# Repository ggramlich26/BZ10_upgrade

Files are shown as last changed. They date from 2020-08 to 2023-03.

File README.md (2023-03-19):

# Bezzera BZ10 Upgrade
This Project is a replacement for the original Bezzera BZ10 electronics bringing many new features including the following:
- Temperature regulation for boiler and brewing unit
- Volumetric brewing system based on water flow instead of time only
- Standby functionality
- Automated wake up from standby, so that the machine is heated up already when you get up in the morning
- Display of various temperatures, volume distributed and distribution time
- Preinfusion (time based)
- WIFI: All parameters (temperatures, distribution volume, wake up time, etc.) can be set with a smartphone or computer
- Automated cleaning cycle: Ten cycles of switching distribution on and off for 20 seconds each by pressing only one button

## Building the project
This project is set up to be built with Eclipse Sloeber, which adds Arduino support to the Eclipse IDE. It uses the following Libraries, which can be installed through the library manager:
- TFT_eSPI (Version 1.4.16)
- Time (Version 1.5.0)
- MCP23017 (Version	1.1.2), not Adafruit MCP23017!
- PID (Version 1.2.0)
- ADS115_WE (Version 1.3.6)
- ArduinoJson (Version 6.19.4)
- ESPmDNS
- SPIFFS

Some libraries are also added as source code. If you use the Arduino IDE, please move all files from the libraries/library name/src/ directly into your project directory. If you use Sloeber, you might have to add the library paths in the project settings: Right click your project/Properties/"C/C++ Build"/Settings. In the Tool Settings Tab, expand the compiler and click Include Folders. Add the following paths ```"${workspace_loc:/BZ10_upgrade/libraries/AsyncTCP/src}"``` and ```"${workspace_loc:/BZ10_upgrade/libraries/ESPAsyncWebServer/src}"``` under each of the three compilers.

**Board settings:** You need to [install the ESP32 board for Sloeber](http://wiki.lauerbach.de/wiki/view.do?page=ESP32Entwicklungsumgebungen). Select NodeMCU-32S as board, Upload Protocol: Default, Flash Frequency: 40MHz, Upload Speed: 115200

***Windows:*** Under windows you need to make sure you have make command installed (e.g. through MinGW64: select mingw32-make package). You might also have to [install CP2102 drivers](https://www.silabs.com/developers/usb-to-uart-bridge-vcp-drivers) if you get a timeout error when trying to upload your sketch.

**Before building** 
You will additionally need to modify User_Setup.h in the TFT_eSPI library folder. Uncomment `#define ILI9341_DRIVER` (line 39) and make sure all other lines in this block are commented out. Then search for the uncommented pin definitions and change them to the following:
```C++
#define TFT_DC 		23
#define TFT_CS 		17
#define	TFT_MOSI	32
#define	TFT_SCLK	33
#define	TFT_MISO	14
#define TFT_RST		16
```

## Setting your WiFi credentials
The machine can be configured to connect to your own home WiFi network via the web interface:
 1. Turn the machine off.
 2. Set the brewing switch to manual mode, hold both buttons pressed (This step resets the wifi configuration. You can omit it if you have a fresh setup).
 3. Turn the machine on while holding the buttons pressed. You can release them once the screen is ready.
 4. Wait for 30 seconds
 5. Connect with any device to the WiFi network "BZ10" with no password required.
 6. Open your web browser and type 192.168.4.1 into address bar, hit enter.
 7. Now you will be presented a prompt to enter the new SSID (your WiFi name) and password. You can also set your machines Bonjour name. Finish by hitting the "Set" button.

## Connecting to the machine
You can connect to the machine with a browser on any device. You can use your computer, smartphone or tablet, for example. Please note: The machine currently **only supports http and not https**. If you cannot connect, you might have to change the line ine your browser to http://your-ip. There are multiple ways to connect:
### Access point mode
When the machine cannot establish a connection to a wifi network, it automatically creates a hotspot after 30 seconds. Simply connect to the network BZ10 with your device. In the browser type in 192.168.4.1 to go to your machine and change the settings.
### Local WiFi
If the machine is connected to your local WiFi network (little wifi icon shown in the bottom), you can reach it by typing its IP in your browser (use your router configuration website to find out what that is and to make it always the same). Alternatively, you can find it with Bonjour. This works out of the box on Apple and Linux machines and requires an extra [installation from the apple resources](https://support.apple.com/downloads/bonjour-for-windows) on windows. You can then reach the machine by typing bz10.local into your browser. If you want to change the address to something else than bz10, you can modify the Bonjour name on the machine website.
## Usage
Your new espresso machine has a lot more functions than before. This is how you can use them
- **Standard manual distribution:** Flip your distribution switch in the manual distribution position for manual dosing and cooling flush
- **True volumetric distribution:** Flip your distribution switch in the volumetric distribution position for automatic dosing. You can set the desired volume via the website. You will also need to set an offset volume that compensates for the water being moved into the brewing unit but not going through your coffee powder. The best way to do so is to measure the difference between set and actual distribution volume and entering this value via Blynk.
- **Preinfusion:** If you set a preinfusion buildup and wait time on the website, volumetric distribution will come with a preinfusion. This is achieved by turning on the pump for the preinfusion buildup time and then waiting for the preinfusion wait time before starting the actual extraction.
- **Cooling flush:** Since the BZ10 is a HX machine, you will still need to perform a cooling flush just like before the upgrade. But in order to make this process more repeatable, you get a timer showing the time passed after your cooling flush. In order to get this functionality, short press the right button before starting your cooling flush. You will see, that the timer starts counting up once you finished your cooling flush.
- **Standby:** Press the left button shortly to enter standby mode. You can also define a period of time after which the machine will automatically enter standby if it has not been used via Blynk.
- **Automated wake up from standby:** Tired of having to wait for half an hour after getting up until you can finally brew your coffee? Just turn your espresso machine on and press the standby button before going to bed. Now you can set a wake up time via the website. If you set it to half an hour before your alarm goes off, your machine will be all ready for your coffee first thing in the morning. This feature only works if wifi is enabled and the machine has connection to the internet, since it needs to get the current time from a remote server.
- **Automated cleaning cycle:** Cleaning is boring and time consuming task. But now you can save a lot of time. Pressing the right button for 3s or more will start an automated cleaning cycle: Your machine will build up pressure for 20s and then release it for another 20s. This process is repeated 10 times.
- **Disable WiFi:** You got everything set up and don't want your machine to be in the internet any more? Nothing easier than that. Just press the left button for 3s or longer. Now you can see the wifi symbol disappearing from the display and once you restart your machine it won't even connect to your WiFi network any more. To enable WiFi again, just press the left button for 3s or longer again. 
- **Display:** Pretty obvious but you now have a display showing various temperatures, the volume distributed and the time your distribution took (preinfusion time not included). The red circle shows the boiler temperature, the orange circle on the right shows the brewing head temperature and the blue circle in the top shows one additional temperature. I attached this sensor to the tube leading from the heat exchanger to the brewing head.

## Code overview
The machine functionality is based on state machines. There are two state machines for boiler and brewing unit temperature control. Another state machine controls the brewing cycle, one is used for the display, and a last one is responsible for the overall machine state including standby functionality. All state machines are visually shown under `/State machines/State machines.odg`. 
In order to make the program more flexible for other hardware, a hardware abstraction class has been written (`dev.c`). Adapting this class will allow the project to run on a different hardware as well.
Besides machine logic, a faster library for TSIC temperature sensors has been developed.
### Brewing state machine
### Boiler heater state machine
### Brewing unit heater state machine
### Display state machine
### Machine status state machine

## The Hardware
There are eagle layout and gerber files available for a PCB designed with this project. You can simply send those files to a manufacturer such as JLCPCB or Seeedstudio. At the moment I also have a few available from my order, that I could have sent to you for very little money. In case you have trouble soldering SMD (surface mounted device) components, we could also discuss having an assembled PCB shipped to you.
### Hardware on the PCB
You will need all need the components listed below to complete the PCB. All of them can be bought from standard suppliers, including Reichelt, Farnell, Mouser etc.

**Resistors:**
|Value|Package | Quantity | Link |
|--|--|--|--
|2.2k|0603|1
|4.7k|0603|2
|10k|0603|2
|22k|0603|3
|47k|0603|2
|100k|0603|1
220k|0603|2
330k|0603|3
1M|0603|1
4.7M|0603|1

**Capacitors:**
|Value|Package | Quantity | Link |
|--|--|--|--
2.2n|0603|1
10n|0603|2
22n|0603|1
100n|0603|2

**Semiconductors:**
|Name|Package | Quantity | Link |
|--|--|--|--
| **Transistors**|
 IRLML5203|MICRO3|1|[farnell](https://de.farnell.com/infineon/irlml5203trpbf/mosfet-p-kanal-30v-3a-sot23/dp/9103511?st=irlml5203)
 BSS138BK|SOT-23|6|[farnell](https://de.farnell.com/nexperia/bss138bk-215/mosfet-n-kanal-60v-0-36a-sot23/dp/2053833?st=bss138bk)
 **Diodes**|
 BAS21|SOT-23|2|[farnell](https://de.farnell.com/diodes-inc/bas21/schaltdiode-250v-0-25w-sot23-3/dp/1902406?st=bas21)
 **ICs**|
 MCP23017SO|SO28W|1|[farnell](https://de.farnell.com/microchip/mcp23017-e-so/16bit-expander-i-o-i2c-i-f-smd/dp/1332087?st=mcp23017)
 NE555D|SO-8|1|[farnell](https://de.farnell.com/texas-instruments/ne555d/precision-timers-linear/dp/3121191?st=ne555d)
 MCP6002-E/SN|SOIC-8|1|[farnell](https://de.farnell.com/microchip/mcp6002-e-sn/op-verst-rker-1mhz-0-6v-us-4500uv/dp/1332118?st=mcp6002-e/sn)
  ADS1115|MSOP10|1|[e.g. from far east](https://www.aliexpress.com/item/32809831068.html?spm=a2g0s.9042311.0.0.27424c4daHnzqu)

**Boards:**
|Name|Package | Quantity | Link |
|--|--|--|--
| ESP32 nodeMCU with external antenna||1|[from far east](https://www.aliexpress.com/item/4000155919030.html?spm=a2g0s.9042311.0.0.27424c4d4ySog2)|

**Power supply:**
|Name|Package | Quantity | Link |
|--|--|--|--
| HLK-PM01 (5V power supply)||1|[from far east](https://www.aliexpress.com/item/4000534910455.html?spm=a2g0s.9042311.0.0.2f024c4dAwDw9T)|

**Connectors:**
|Name|rows|positions|m/f| Quantity | Comment |
|--|--|--|--|--|--
pinheader 2.54mm|1|2|f+m|4|boiler SSR, boiler probe, NTC, tank switch
pinheader 2.54mm|1|3|f+m|5|connecting TSIC temperature and flow sensors
pinheader 2.54mm|1|6|f+m|2|connecting arduino SSR board
pinheader 2.54mm|1|8|f+m|2|connecting switches and LEDs
pinheader 2.54mm|1|9|f+m|2|display
wire to board connectors, RM5 with screws|1|2|f|1|230V connector [farnell](https://de.farnell.com/camdenboss/ctb1500-2/terminal-block-5mm-2-way/dp/3377326?st=wire%20to%20board%20rm5)

### Hardware off the PCB in the machine
- Arduino SSR board with 4 SSRs (e.g. [Arduino SSR module on Amazon](https://www.amazon.de/Ecloud-4-Channel-Trigger-SSR-Modul-Brett-Arduino-resistivem/dp/B01E6KUMTI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))
- One SSRs for 230V, switchable by 3-5VDC (called SSR-40 DA) for boiler heater and electric brewing unit heater (e.g. [SSR on Amazon](https://www.amazon.de/KKmoon-24V-380V-SSR-40-Relaismodul-Temperaturregler/dp/B010Q6898C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))
- SPI TFT Display 320x240 Pixels with ILI9341 (e.g. [Display on Amazon](https://www.amazon.de/gp/product/B01E0MGZU2/ref=ppx_yo_dt_b_asin_title_o09_s00?ie=UTF8&psc=1))
- Alternative switches: Brewing switch should be replaced by a 3 fixed positions switch, indicator lights should be replaced by push buttons with LEDs, so that they can serve as indicator lights and inputs at the same time. (I used [those](https://www.aliexpress.com/item/4000454624299.html?spm=a2g0s.9042311.0.0.27424c4dZZ9bgU) instead of the indicator lights (3-6V, momentary version) and [those](https://www.aliexpress.com/item/4000028451024.html?spm=a2g0s.9042311.0.0.27424c4dZZ9bgU) for the original two push buttons (5V, latching fixation, blue LED, 2 positions for on/off, 3 positions for brewing switch). If you want to use those switches for on/off, you will need to add a relay in the power supply chain because they are not strong enough for the entire espresso machine power!
- TSIC 306 temperature sensors, 3 pieces
- Flow sensors, 2 pieces (e.g. [from far east](https://www.aliexpress.com/item/32949504762.html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,searchweb201602_,searchweb201603_))
- Quite some wiring. I chose Oelflex Heat for its heat resistance up to 180°C (purchased from Conrad electronics)

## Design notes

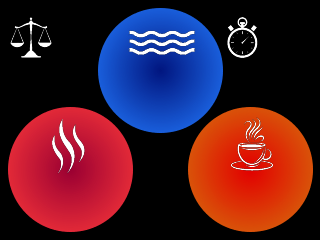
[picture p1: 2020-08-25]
Bilder/Background_V2.png

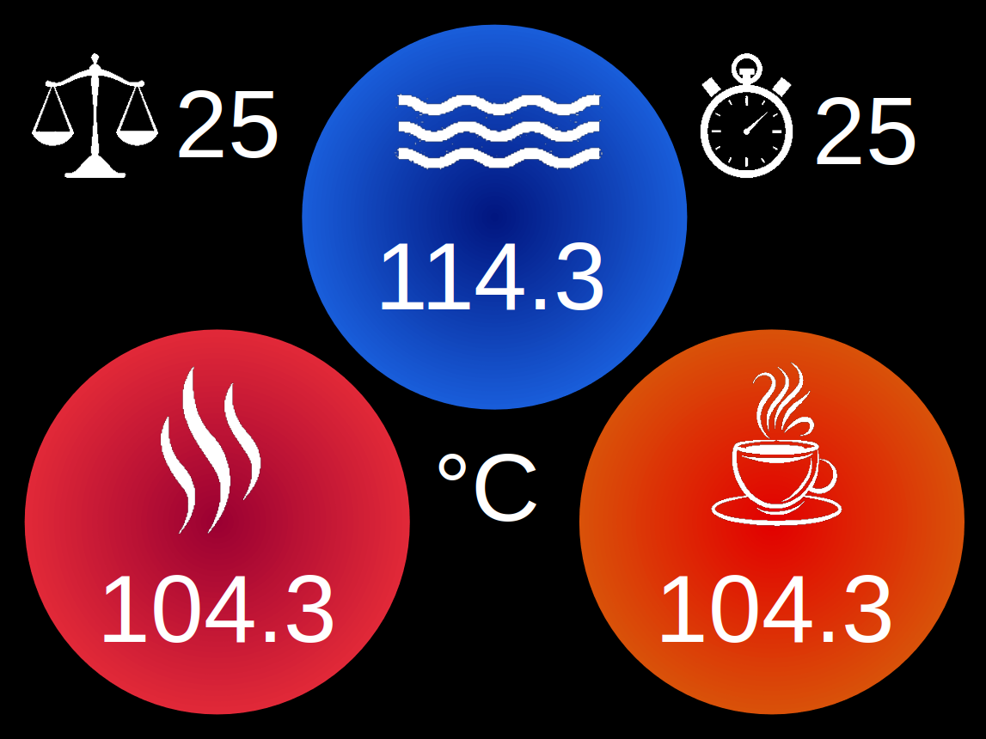
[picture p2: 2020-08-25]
Bilder/Background_V2_with_text.png

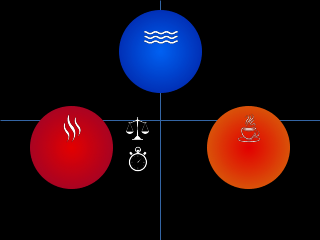
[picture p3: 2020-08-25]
Bilder/Background.png

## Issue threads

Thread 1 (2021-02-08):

TSIC 306 Placement

smoki3, 2021-02-08:
Hi,

very nice project. Could you share a picture where and how you have assembled the TSIC 306? Especially on the boiler and the HX?

ggramlich26, 2021-02-15:
Hi,
thank you. I just added the photos under "images mod/".
I used thermally conductive glue to attach the TSICs and zip ties to hold them in place until the glue had dried. Then I insulated them with mineral wool which I attached with kapton tape (that actually makes a difference of multiple degrees in the measurements).
For the brewing unit I glued the TSIC to a small disk, which I then screwed onto it intead of the original bimetal switch. That's just to sure I could undo my changes in the worst case.
The temperature sensor on the pipe from HX to brewing head is not a big help unfortunately, because the tube slows its reaction down too much. One would probably need to place a sensor inside the tube or the HX boiler itself to get precise measurements.

smoki3, 2021-02-15:
Okay thanks for the pictures :) How is your experience with the temp sensor outside the boiler? The BZ07 for example uses a tube which goes into the boiler to measure the temperatur

Do you also have the layout ready for the pcb, or you maybe have one pcb remaining?  I also bought a BZ10 and want to mod it too.

ggramlich26, 2021-02-18:
A temp sensor inside the boiler certainly is the better option but it I didn't want to dril a hole in my boiler. Placing the sensor outside the boiler adds a noticable latency.

I can add the layout for the PCB but the current version still uses an ESP32 board with integrated antenna. Since the metallic case of the machine acts as a faraday cage, you'd have very bad intenet connection in there. I just cut the antenna off and soldered a coaxial wire with SMA connector to it. I then lead it out of the machine and attached a regula WiFi antenna.
I can also send you a PCB. I think I have four left atm.

Reisediel, 2023-01-21:
I got a BZ10 shortly and I want to mod it. For temp measurement inside the boiler you can unscrew screw #1 and replace it with an 1/4" probe like in the boiler from a BZ07.
https://www.avola-coffeesystems.de/bezzera/bezzera-bz10-heizung/8279034

smoki3, 2023-01-21:
Yes correctly

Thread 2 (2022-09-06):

Capacity C7 / C8

smoki3, 2022-09-06:
Hi,

do you know the value of the capacity c7/c8?

ggramlich26, 2022-09-08:
Hi,

I had paced them there to have the possibility to smoothen the temperature sensor voltages in case there was a lot of noise coming from the power supply etc but didn't end up using them. You can leave them empty, that's why there are no values given.

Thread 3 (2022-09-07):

Blynk Legacy wird abgeschaltet.

smoki3, 2022-09-07:
Hi,

das bisher genutzte Blynk wird ja bald abgeschaltet. Hast du dir schon eine alternative überlegt oder auf das neue zu migrieren?

ggramlich26, 2022-09-08:
Hi,

ja, das ist mir leider auch schon aufgefallen. Ich will eigentlich nicht auf das neue migrieren, weil das in einem Abo-Modell läuft und mir das einfach zu teuer ist, ich hatte aber auch noch keine Zeit mich um eine gute Alternative zu kümmern. Hast du zufällig eine Idee?

smoki3, 2022-09-08:
Ich bin nun auf das neue migriert. Gibt ein paar Widget die kostenlos sind. Ich benutze hauptsächlich den Slider. Kann in meinem Fork anschauen.

smoki3, 2022-09-08:
So sieht das ganze dann aus:

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

ggramlich26, 2022-09-13:
Das sieht gut aus! Und davon ist noch alles kostenlos?

smoki3, 2022-09-13:
Ja genau dafür musste ich nun gar nix bezahlen. Eine ganze Reihe kostenloser Widget. Damit lässt sich die Steuerung ganz gut realisieren.

Das ist die Mobile Ansicht:

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

ggramlich26, 2022-09-14:
Perfekt, was will ich mehr! Dann werde ich mal in deinen code reinschauen für die Portierung und mich bis Ende des Jahres darum kümmern selbst auch umzusteigen. Danke für die Idee!

smoki3, 2022-09-14:
Am code ändert sich eigentlich nichts. Außer die Zugangsdaten müssen ergänzt werden und die aktuelle Library

smoki3, 2022-09-14:
Die meiste Arbeit ist das Anlegen des Templates

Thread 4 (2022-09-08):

Widerstände Boiler Füllstand

smoki3, 2022-09-08:
Hi,

ich wollte nun auch auf die neue Platine umsteigen. Allerdings funktioniert bei mir die Füllstandsonde nicht mehr.

Nun hab ich in LTSpice, Board V2 und V3 jeweils unterschiedliche Werte. Kann du mir da einwenig Licht ins dunkle bringen und mir die Korrekten werte nennen?

smoki3, 2022-09-13:
Konnte es inzwischen beheben. War wohl irgendwo ein falscher Widerstand

ggramlich26, 2022-09-14:
Super, das freut mich!

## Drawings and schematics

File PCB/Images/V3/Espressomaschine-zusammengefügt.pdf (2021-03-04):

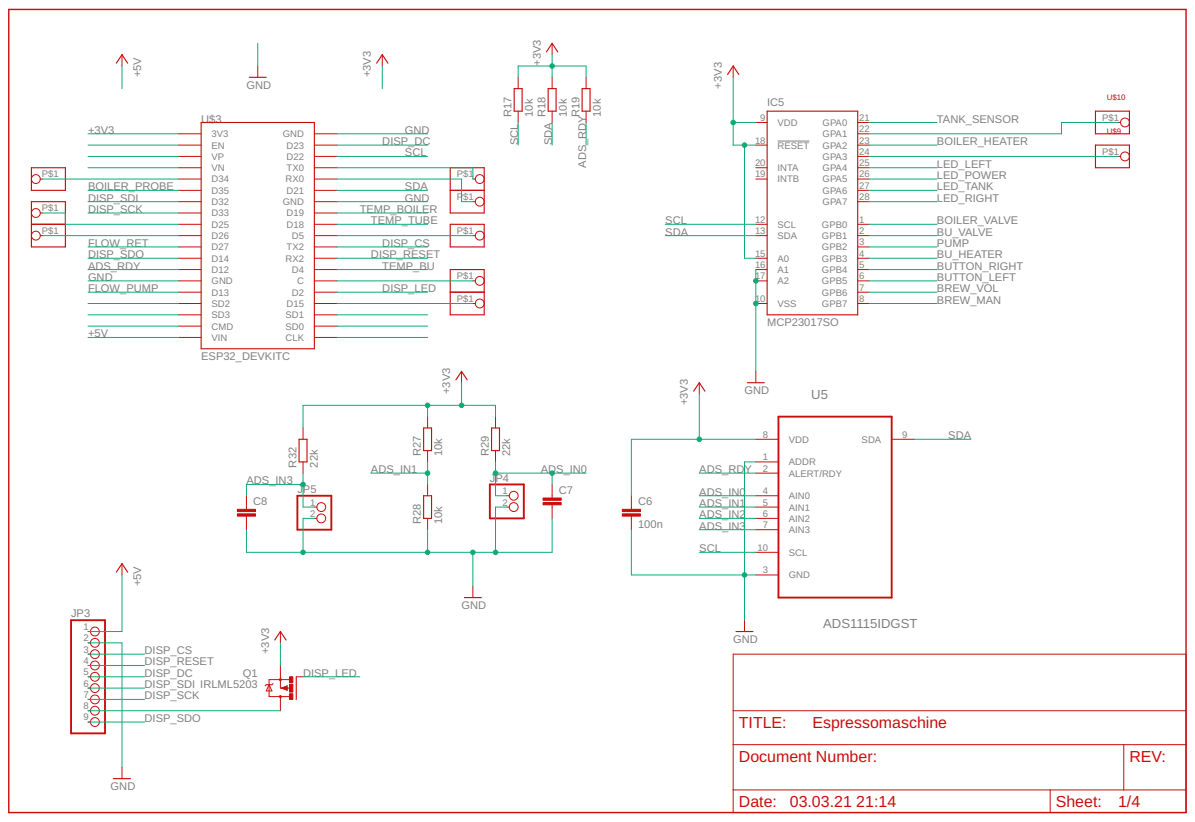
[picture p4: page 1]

Document Number: | REV:

Date: 03.03.21 21:14 | Sheet: 1/4

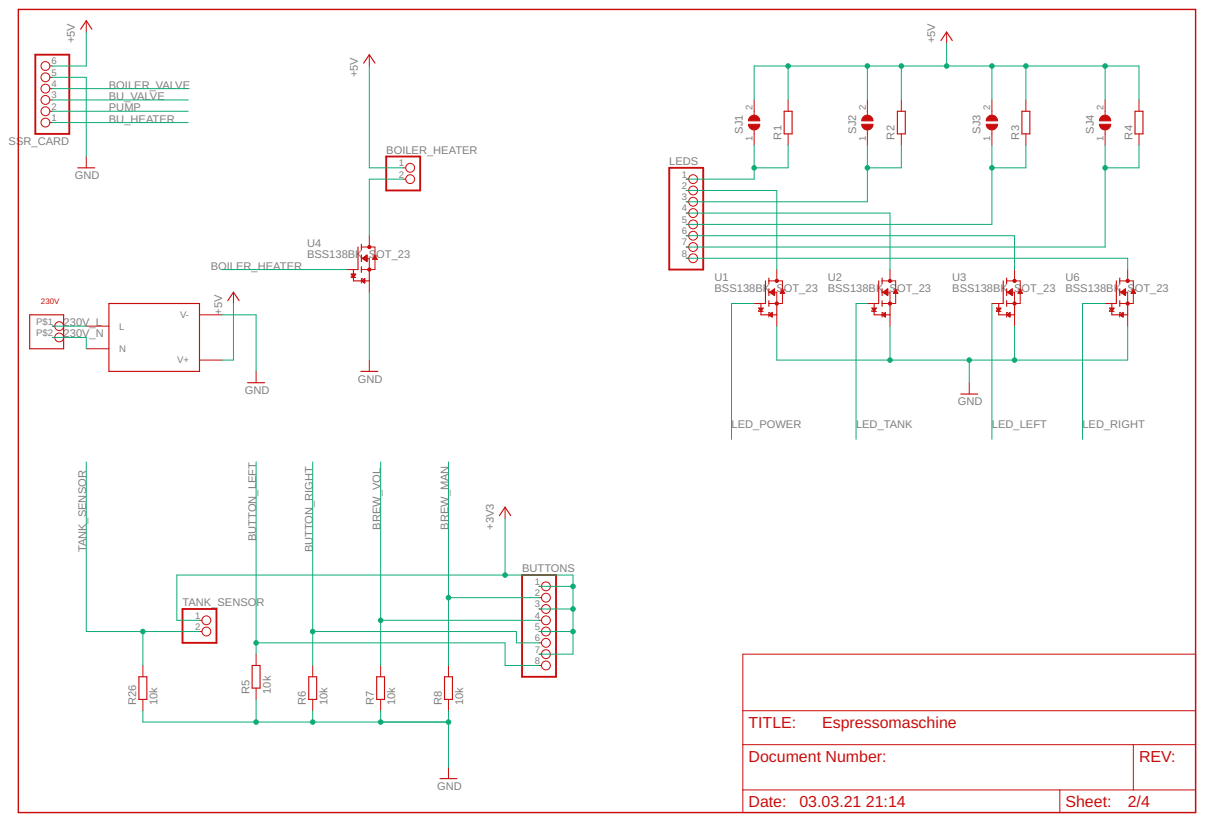
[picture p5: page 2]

Document Number: | REV:

Date: 03.03.21 21:14 | Sheet: 2/4

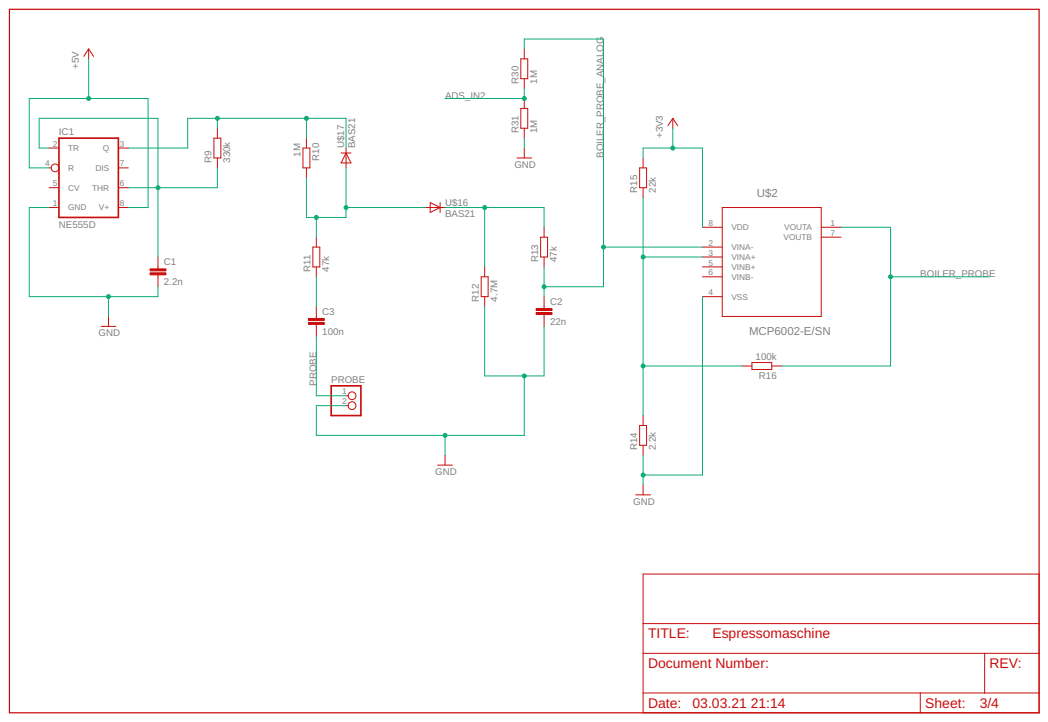
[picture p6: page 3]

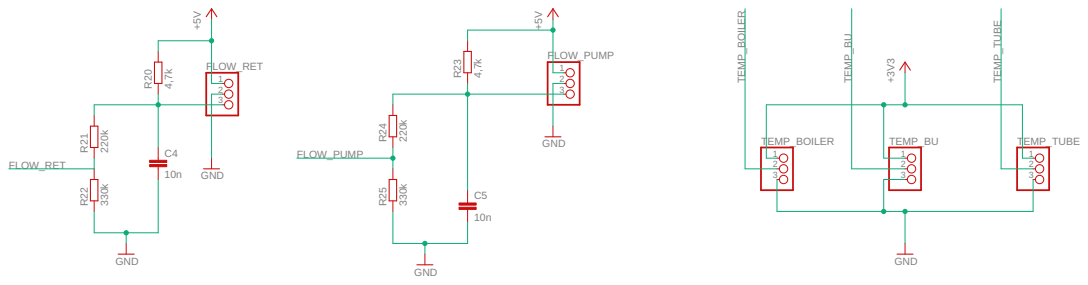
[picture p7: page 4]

Document Number: | REV:

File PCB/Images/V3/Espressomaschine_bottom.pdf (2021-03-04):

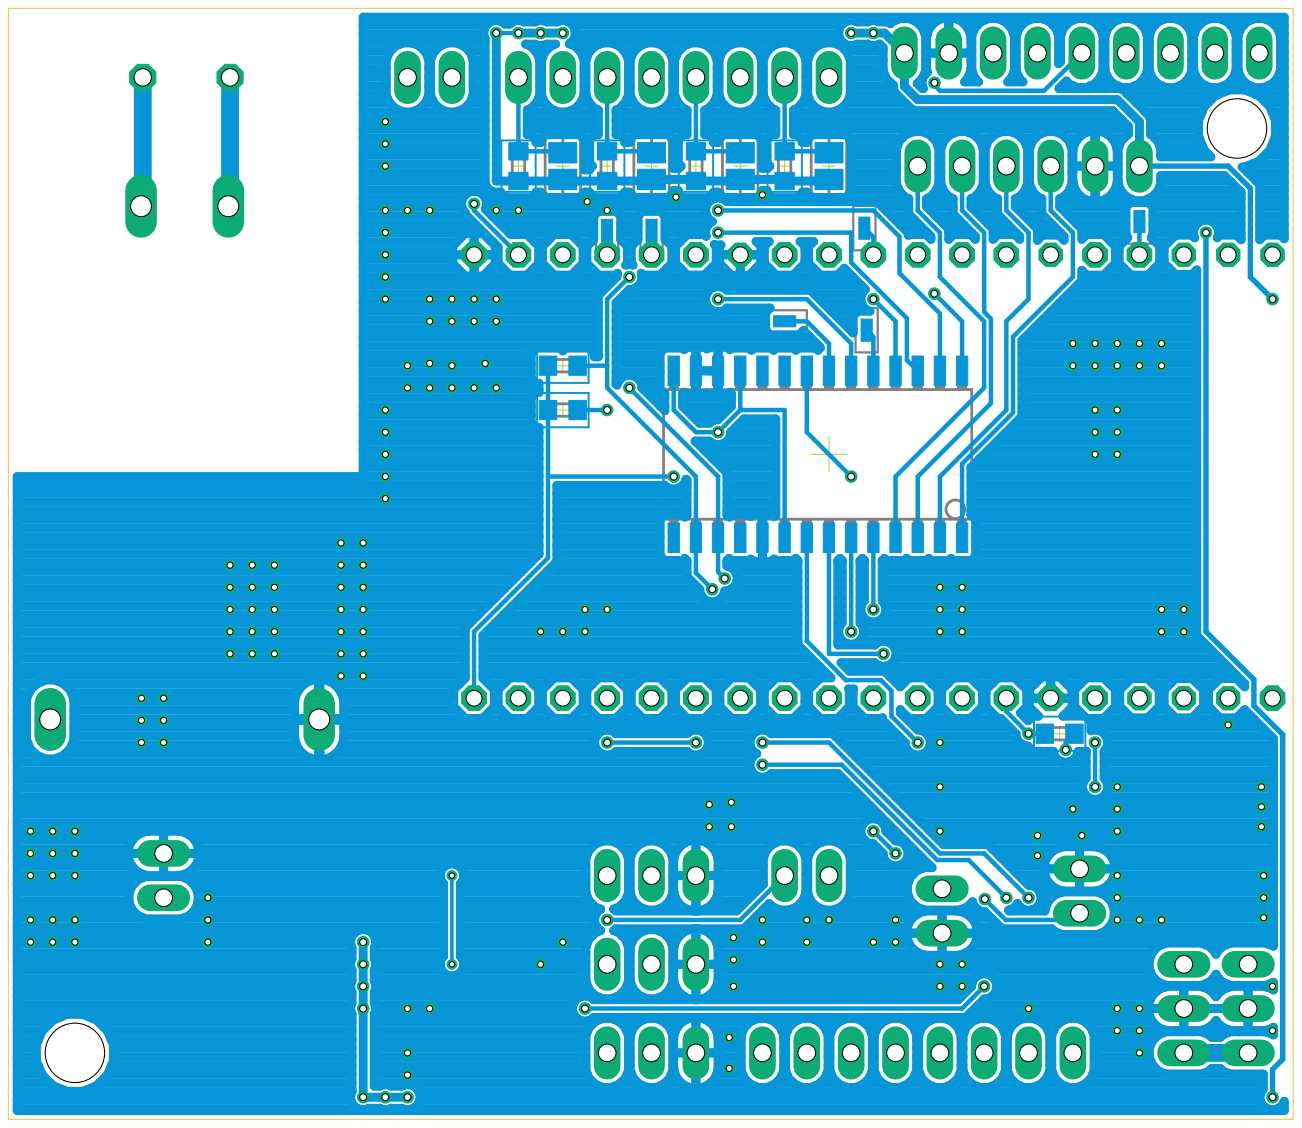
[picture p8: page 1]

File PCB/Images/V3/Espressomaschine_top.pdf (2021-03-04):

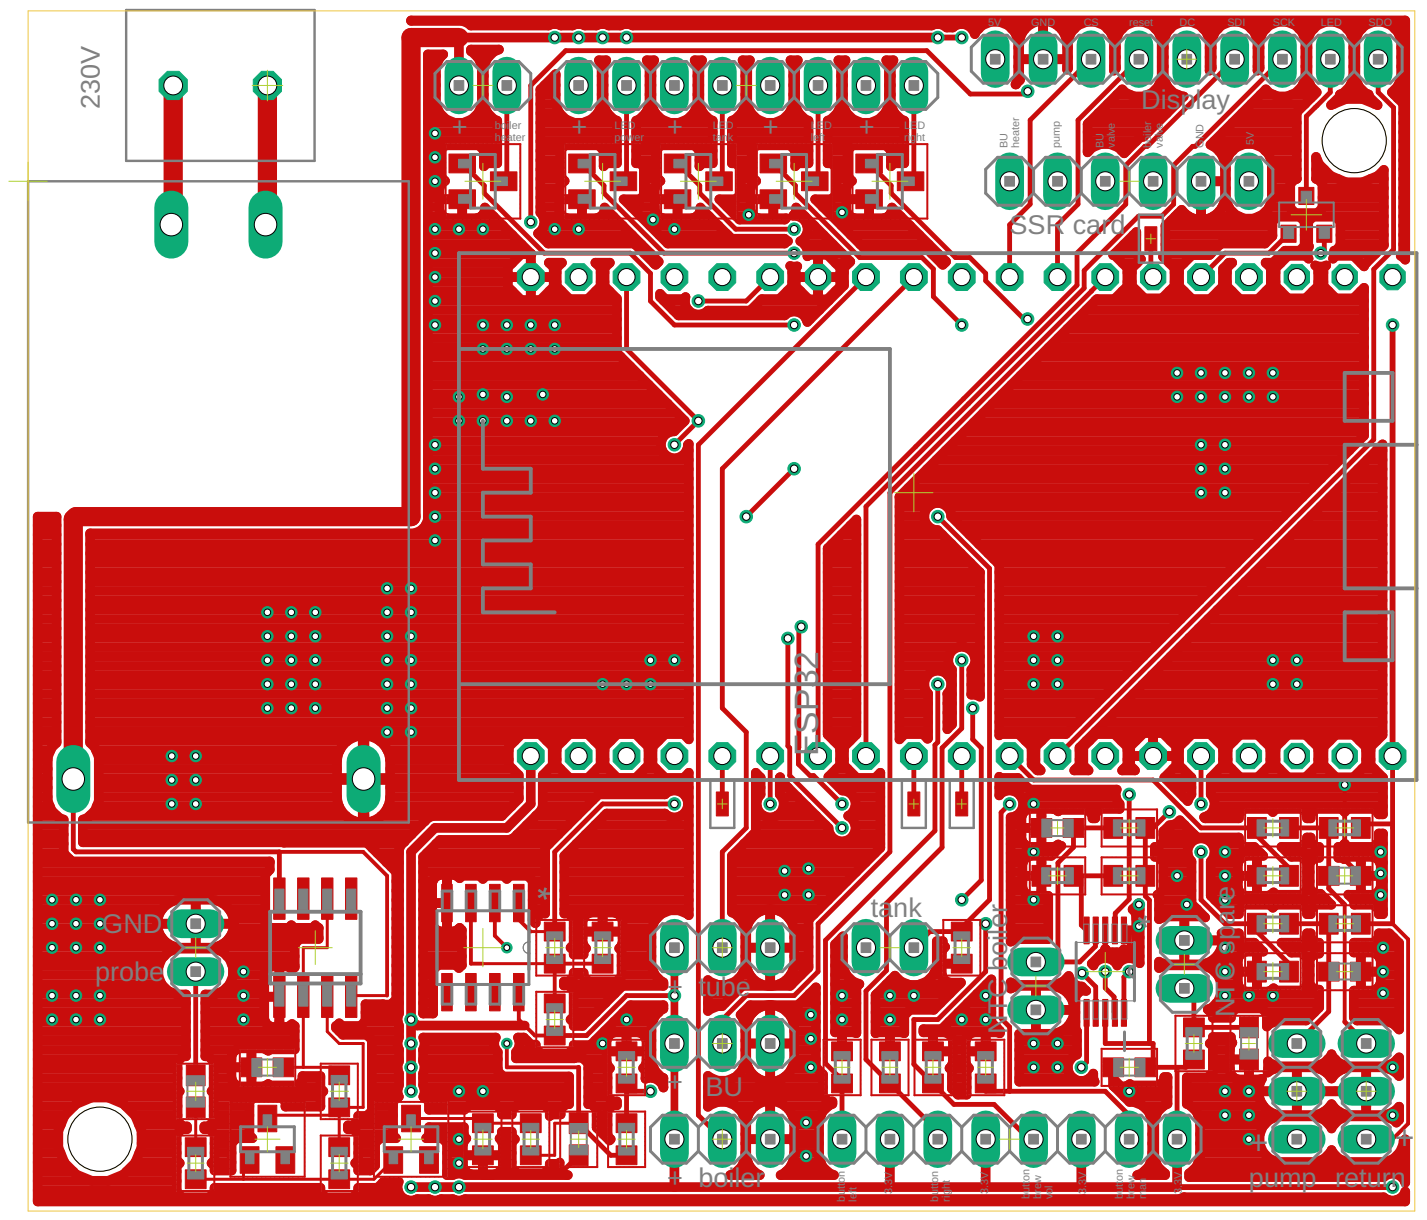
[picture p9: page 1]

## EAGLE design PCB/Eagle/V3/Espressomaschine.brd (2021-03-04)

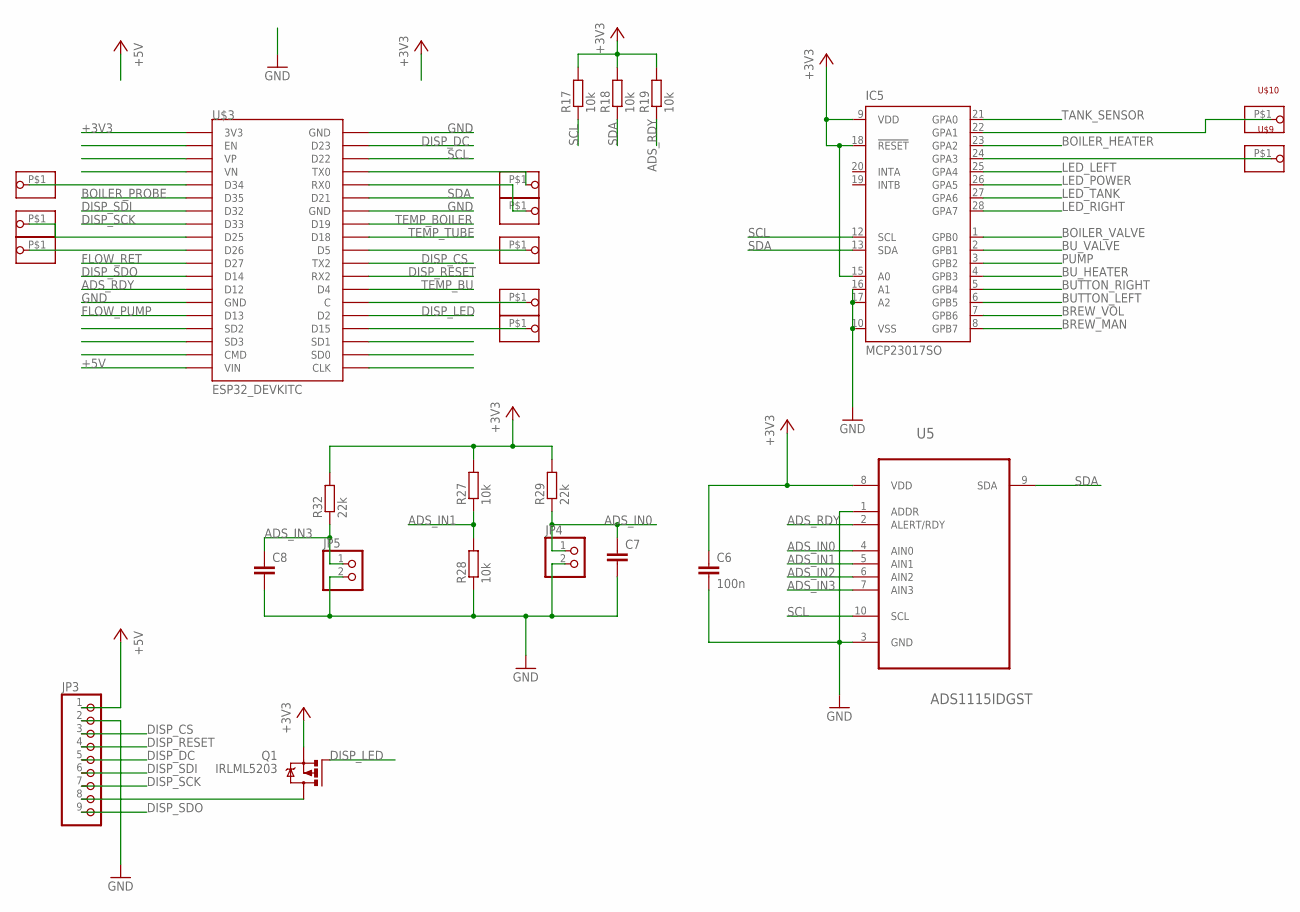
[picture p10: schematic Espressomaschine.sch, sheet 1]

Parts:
C6: 100n; C0603
C7, C8: C-EUC0603; C0603
IC5: MCP23017SO; SO28W
JP3: PINHD-1X9; 1X09
JP4, JP5: PINHD-1X2; 1X02
Q1: IRLML5203; MICRO3
R17, R18, R19, R27, R28: 10k; R0603
R29, R32: 22k; R0603
U5: ADS1115IDGST; SOP50P490X110-10N
U$3: ESP32_DEVKITC
U$5, U$6, U$7, U$8, U$9, U$10, U$11, U$12, U$13, U$14: PINHD-1X1SMD_RM1.27; 1X01_SMD_RM1.27

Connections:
+3V3: C6.1, IC5.9 (VDD), IC5.15 (A0), IC5.18 (!RESET), Q1.2 (S), R17.2, R18.2, R19.2, R27.2, R29.2, R32.2, U5.8 (VDD), U$3.3V3; also elsewhere on the board
+5V: JP3.1, U$3.VIN; also elsewhere on the board
ADS_IN0: C7.1, JP4.1, R29.1, U5.4 (AIN0)
ADS_IN1: R27.1, R28.2, U5.5 (AIN1)
ADS_IN2: U5.6 (AIN2); also elsewhere on the board
ADS_IN3: C8.1, JP5.1, R32.1, U5.7 (AIN3)
ADS_RDY: R19.1, U5.2 (ALERT/RDY), U$3.D12
BOILER_HEATER: IC5.23 (GPA2); also elsewhere on the board
BOILER_PROBE: U$3.D35; also elsewhere on the board
BOILER_VALVE: IC5.1 (GPB0); also elsewhere on the board
BREW_MAN: IC5.8 (GPB7); also elsewhere on the board
BREW_VOL: IC5.7 (GPB6); also elsewhere on the board
BUTTON_LEFT: IC5.6 (GPB5); also elsewhere on the board
BUTTON_RIGHT: IC5.5 (GPB4); also elsewhere on the board
BU_HEATER: IC5.4 (GPB3); also elsewhere on the board
BU_VALVE: IC5.2 (GPB1); also elsewhere on the board
DISP_CS: JP3.3, U$3.TX2
DISP_DC: JP3.5, U$3.D23
DISP_LED: Q1.1 (G), U$3.D2
DISP_RESET: JP3.4, U$3.RX2
DISP_SCK: JP3.7, U$3.D33
DISP_SDI: JP3.6, U$3.D32
DISP_SDO: JP3.9, U$3.D14
FLOW_PUMP: U$3.D13; also elsewhere on the board
FLOW_RET: U$3.D27; also elsewhere on the board
GND: C6.2, C7.2, C8.2, IC5.10 (VSS), IC5.16 (A1), IC5.17 (A2), JP3.2, JP4.2, JP5.2, R28.1, U5.1 (ADDR), U5.3 (GND), U$3.GND@1 (GND), U$3.GND@2 (GND), U$3.GND@3 (GND); also elsewhere on the board
LED_LEFT: IC5.25 (GPA4); also elsewhere on the board
LED_POWER: IC5.26 (GPA5); also elsewhere on the board
LED_RIGHT: IC5.28 (GPA7); also elsewhere on the board
LED_TANK: IC5.27 (GPA6); also elsewhere on the board
unnamed: U$3.C, U$7.P$1
unnamed: IC5.22 (GPA1), U$10.P$1
unnamed: IC5.24 (GPA3), U$9.P$1
unnamed: U$3.TX0, U$5.P$1
unnamed: JP3.8, Q1.3 (D)
unnamed: U$3.RX0, U$11.P$1
unnamed: U$3.D5, U$6.P$1
unnamed: U$3.D15, U$8.P$1
unnamed: U$3.D34, U$12.P$1
unnamed: U$3.D25, U$13.P$1
unnamed: U$3.D26, U$14.P$1
PUMP: IC5.3 (GPB2); also elsewhere on the board
SCL: IC5.12 (SCL), R17.1, U5.10 (SCL), U$3.D22
SDA: IC5.13 (SDA), R18.1, U5.9 (SDA), U$3.D21
TANK_SENSOR: IC5.21 (GPA0); also elsewhere on the board
TEMP_BOILER: U$3.D19; also elsewhere on the board
TEMP_BU: U$3.D4; also elsewhere on the board
TEMP_TUBE: U$3.D18; also elsewhere on the board

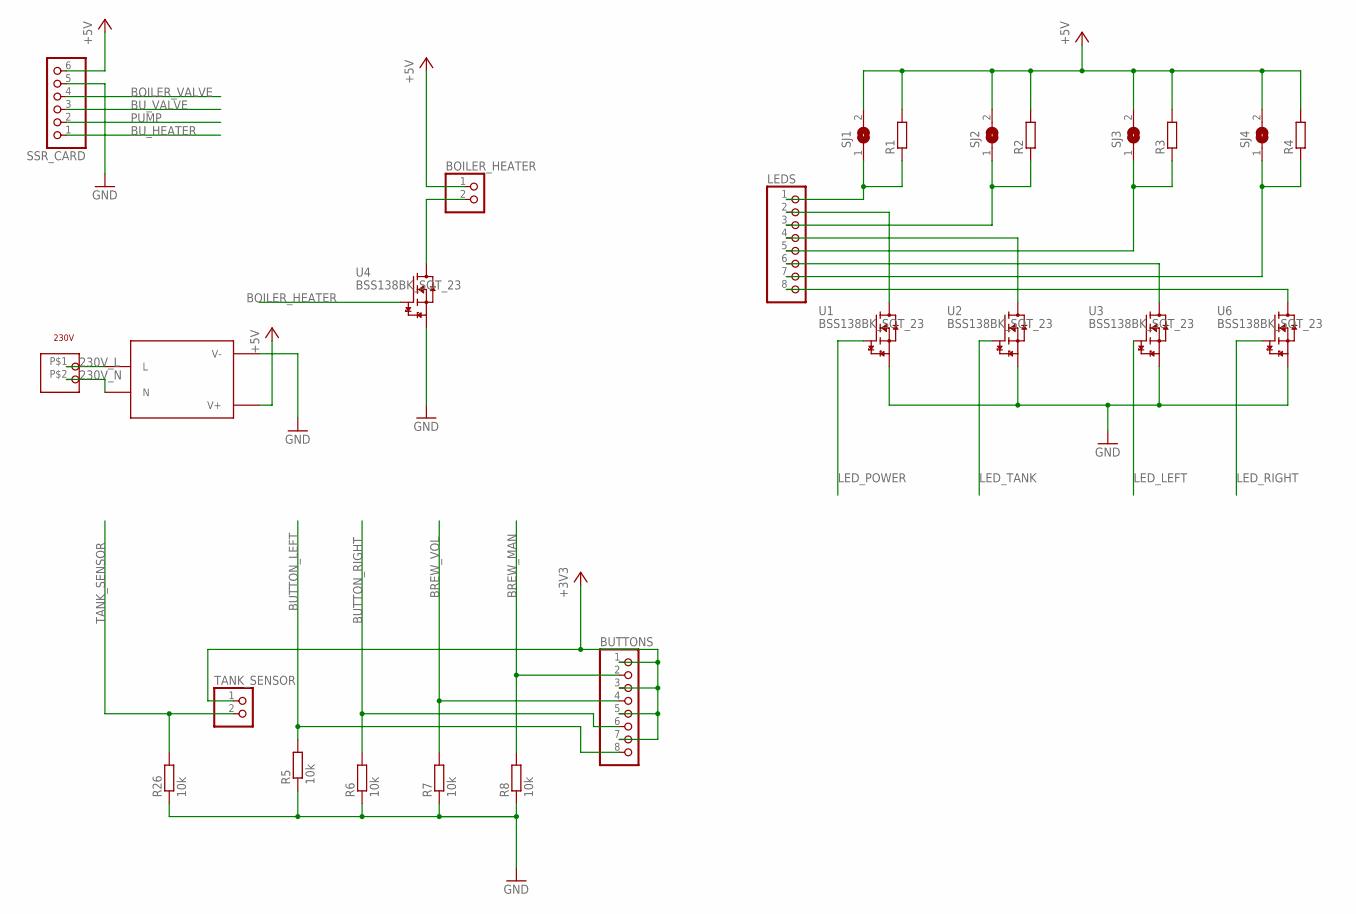
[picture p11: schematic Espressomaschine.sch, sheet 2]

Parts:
230V: 1X2RM5; 1X02_RM5
BOILER_HEATER: PINHD-1X2; 1X02
BUTTONS: PINHD-1X8; 1X08
LEDS: PINHD-1X8; 1X08
R1, R2, R3, R4: R-EU_R0603; R0603
R5, R6, R7, R8, R26: 10k; R0603
SJ1, SJ2, SJ3, SJ4: SJ
SSR_CARD: PINHD-1X6; 1X06
TANK_SENSOR: PINHD-1X2; 1X02
U1, U2, U3, U4, U6: BSS138BK_SOT_23; SOT23
U$1: HLK-PM0X

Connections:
230V_L: 230V.P$1 (1), U$1.L
230V_N: 230V.P$2 (2), U$1.N
+3V3: BUTTONS.1, BUTTONS.3, BUTTONS.5, BUTTONS.7, TANK_SENSOR.1; also elsewhere on the board
+5V: BOILER_HEATER.1, R1.2, R2.2, R3.2, R4.2, SJ1.2, SJ2.2, SJ3.2, SJ4.2, SSR_CARD.6, U$1.V+; also elsewhere on the board
BOILER_HEATER: U4.1 (G); also elsewhere on the board
BOILER_VALVE: SSR_CARD.4; also elsewhere on the board
BREW_MAN: BUTTONS.2, R8.2; also elsewhere on the board
BREW_VOL: BUTTONS.4, R7.2; also elsewhere on the board
BUTTON_LEFT: BUTTONS.8, R5.2; also elsewhere on the board
BUTTON_RIGHT: BUTTONS.6, R6.2; also elsewhere on the board
BU_HEATER: SSR_CARD.1; also elsewhere on the board
BU_VALVE: SSR_CARD.3; also elsewhere on the board
GND: R5.1, R6.1, R7.1, R8.1, R26.1, SSR_CARD.5, U1.2 (S), U2.2 (S), U3.2 (S), U4.2 (S), U6.2 (S), U$1.V-; also elsewhere on the board
LED_LEFT: U3.1 (G); also elsewhere on the board
LED_POWER: U1.1 (G); also elsewhere on the board
LED_RIGHT: U6.1 (G); also elsewhere on the board
LED_TANK: U2.1 (G); also elsewhere on the board
unnamed: LEDS.1, R1.1, SJ1.1
unnamed: LEDS.3, R2.1, SJ2.1
unnamed: LEDS.5, R3.1, SJ3.1
unnamed: LEDS.8, U6.3 (D)
unnamed: LEDS.6, U3.3 (D)
unnamed: BOILER_HEATER.2, U4.3 (D)
unnamed: LEDS.7, R4.1, SJ4.1
unnamed: LEDS.4, U2.3 (D)
unnamed: LEDS.2, U1.3 (D)
PUMP: SSR_CARD.2; also elsewhere on the board
TANK_SENSOR: R26.2, TANK_SENSOR.2; also elsewhere on the board

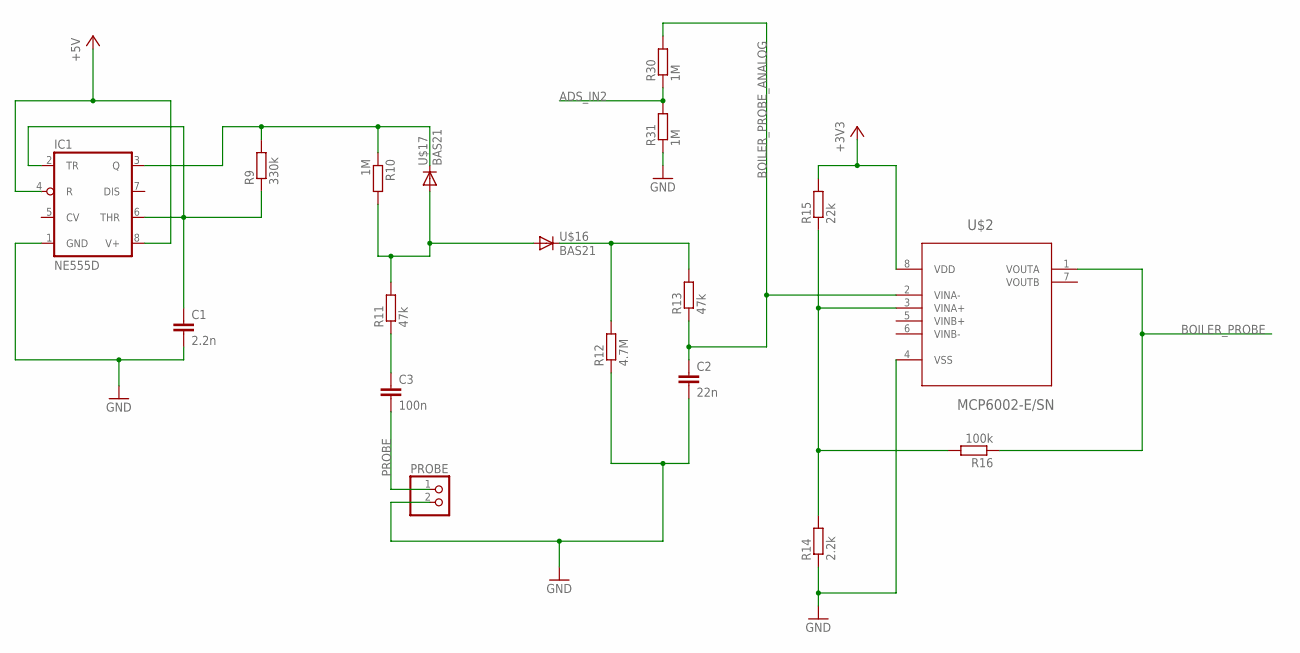
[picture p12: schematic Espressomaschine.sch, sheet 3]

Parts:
C1: 2.2n; C0603
C2: 22n; C0603
C3: 100n; C0603
IC1: NE555D; SO08
PROBE: PINHD-1X2; 1X02
R9: 330k; R0603
R10, R30, R31: 1M; R0603
R11, R13: 47k; R0603
R12: 4.7M; R0603
R14: 2.2k; R0603
R15: 22k; R0603
R16: 100k; R0603
U$2: MCP6002-E/SN; SOIC127P600X175-8N
U$16, U$17: BAS21; SOT23

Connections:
+3V3: R15.2, U$2.8 (VDD); also elsewhere on the board
+5V: IC1.4 (R), IC1.8 (V+); also elsewhere on the board
ADS_IN2: R30.1, R31.2; also elsewhere on the board
BOILER_PROBE: R16.1, U$2.1 (VOUTA); also elsewhere on the board
BOILER_PROBE_ANALOG: C2.1, R13.1, R30.2, U$2.2 (VINA-)
GND: C1.2, C2.2, IC1.1 (GND), PROBE.2, R12.1, R14.1, R31.1, U$2.4 (VSS); also elsewhere on the board
unnamed: C1.1, IC1.2 (TR), IC1.6 (THR), R9.1
unnamed: R10.2, R11.2, U$16.1 (A), U$17.1 (A)
unnamed: C3.1, R11.1
unnamed: IC1.3 (Q), R9.2, R10.1, U$17.3 (C)
unnamed: R12.2, R13.2, U$16.3 (C)
unnamed: R14.2, R15.1, R16.2, U$2.3 (VINA+)
PROBE: C3.2, PROBE.1

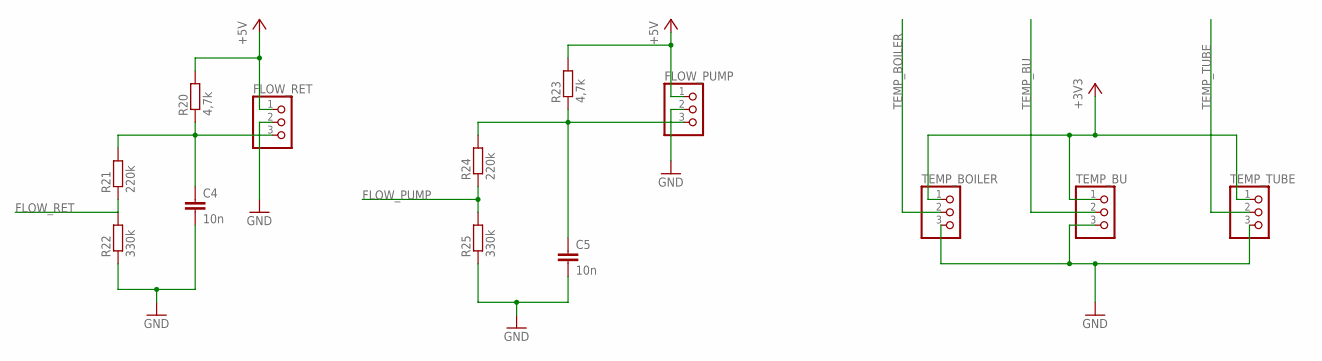
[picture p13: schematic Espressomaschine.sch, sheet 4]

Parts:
C4, C5: 10n; C0603
FLOW_PUMP: PINHD-1X3; 1X03
FLOW_RET: PINHD-1X3; 1X03
R20, R23: 4,7k; R0603
R21, R24: 220k; R0603
R22, R25: 330k; R0603
TEMP_BOILER: PINHD-1X3; 1X03
TEMP_BU: PINHD-1X3; 1X03
TEMP_TUBE: PINHD-1X3; 1X03

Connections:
+3V3: TEMP_BOILER.1, TEMP_BU.1, TEMP_TUBE.1; also elsewhere on the board
+5V: FLOW_PUMP.1, FLOW_RET.1, R20.2, R23.2; also elsewhere on the board
FLOW_PUMP: R24.1, R25.2; also elsewhere on the board
FLOW_RET: R21.1, R22.2; also elsewhere on the board
GND: C4.2, C5.2, FLOW_PUMP.2, FLOW_RET.2, R22.1, R25.1, TEMP_BOILER.3, TEMP_BU.3, TEMP_TUBE.3; also elsewhere on the board
unnamed: C4.1, FLOW_RET.3, R20.1, R21.2
unnamed: C5.1, FLOW_PUMP.3, R23.1, R24.2
TEMP_BOILER: TEMP_BOILER.2; also elsewhere on the board
TEMP_BU: TEMP_BU.2; also elsewhere on the board
TEMP_TUBE: TEMP_TUBE.2; also elsewhere on the board

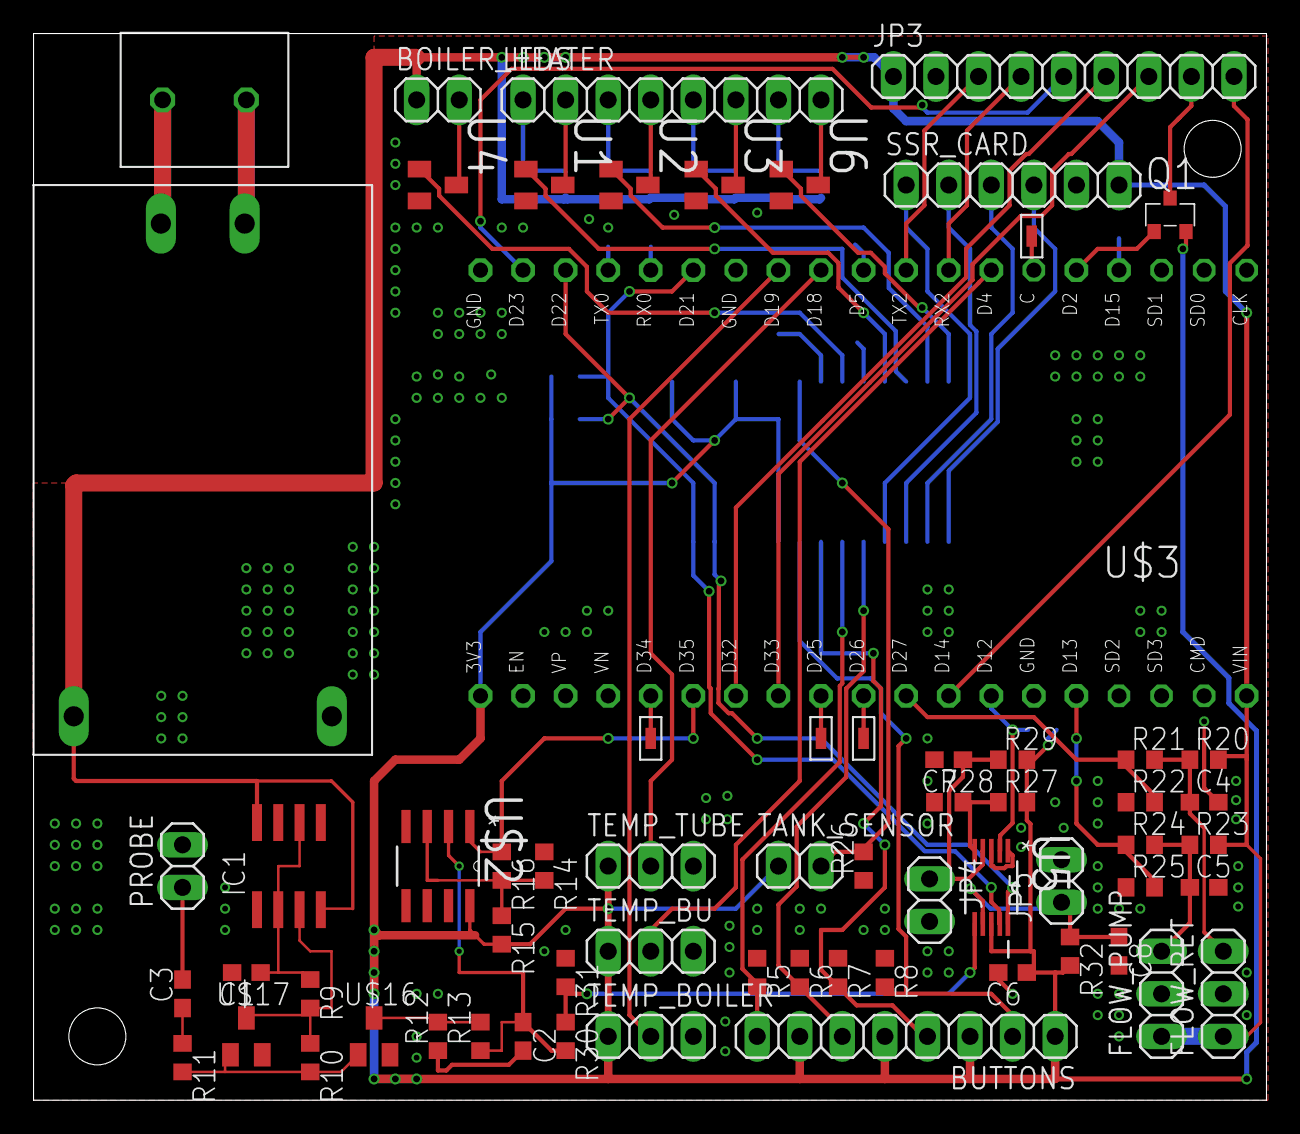
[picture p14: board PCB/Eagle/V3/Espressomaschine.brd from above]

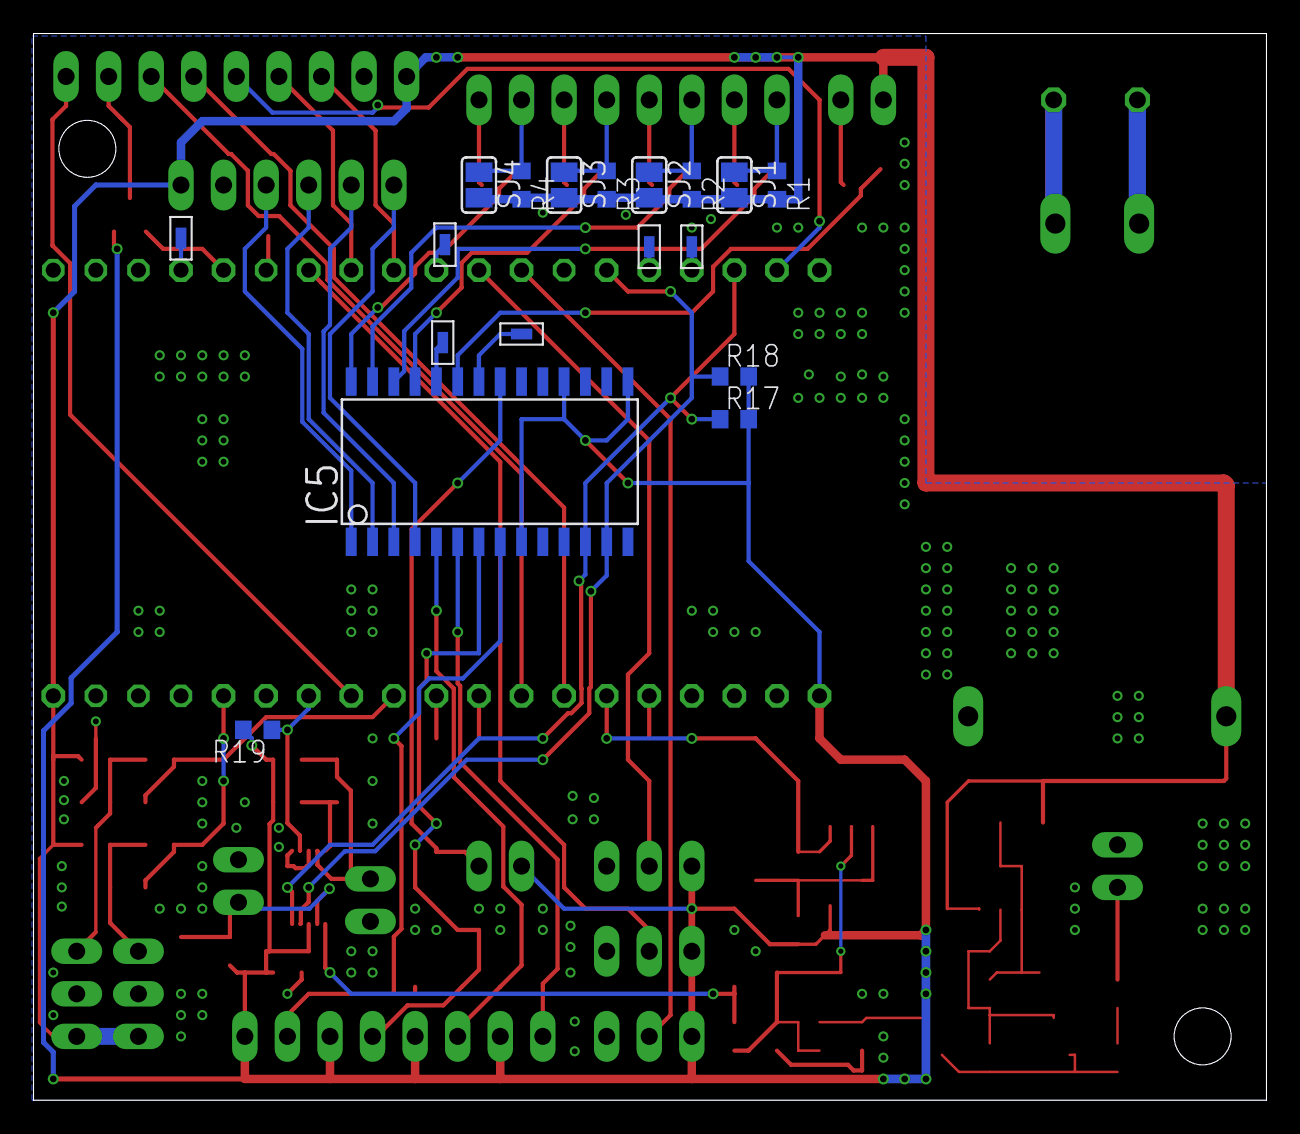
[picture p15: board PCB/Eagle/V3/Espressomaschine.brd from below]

Board: 2 copper layers, 73.6 x 63.6 mm, 83 parts (18 on the bottom side), 69 nets.

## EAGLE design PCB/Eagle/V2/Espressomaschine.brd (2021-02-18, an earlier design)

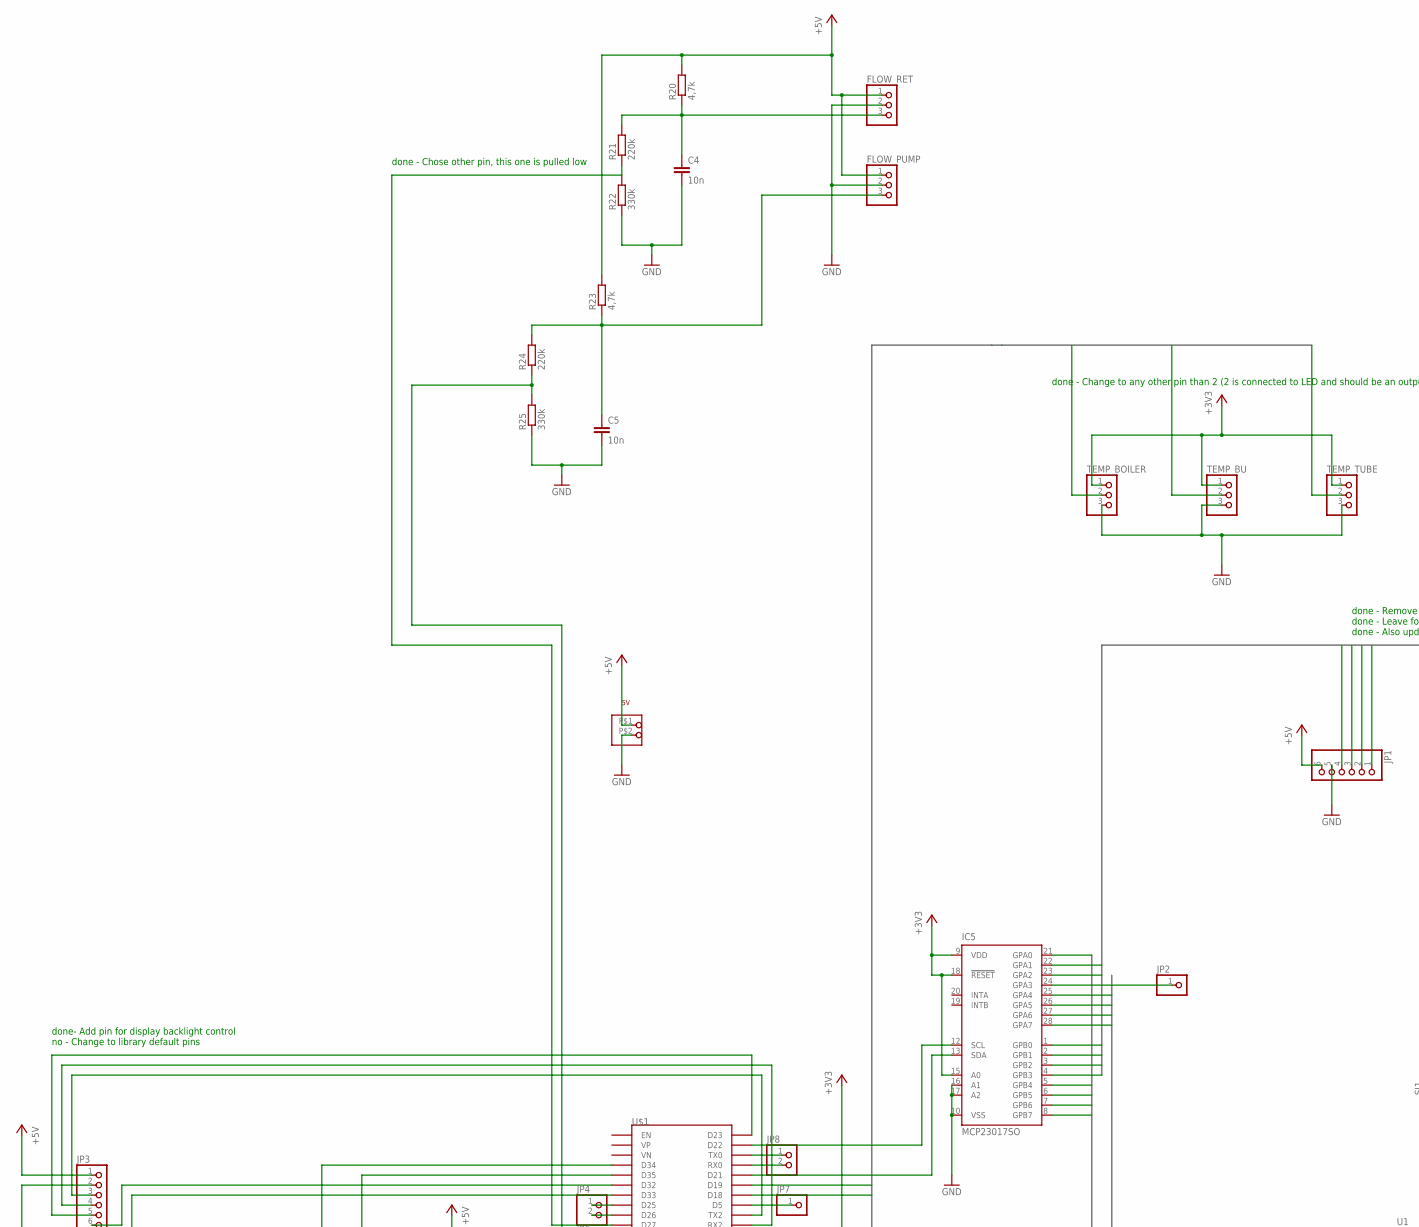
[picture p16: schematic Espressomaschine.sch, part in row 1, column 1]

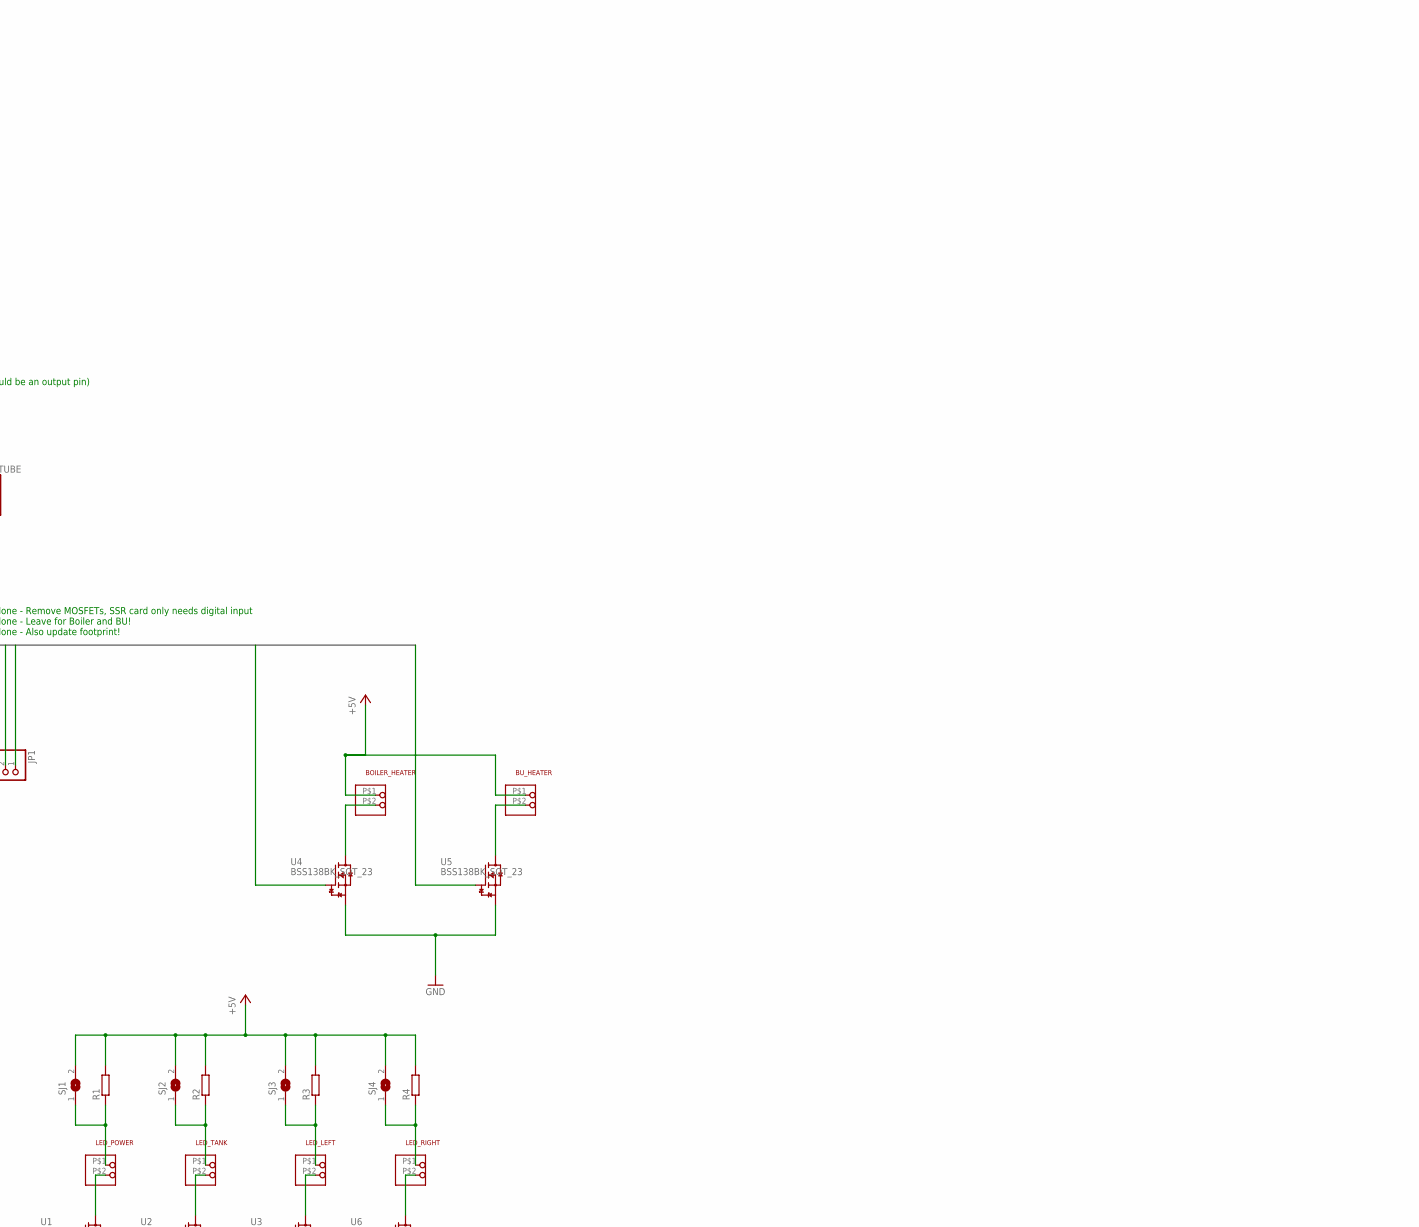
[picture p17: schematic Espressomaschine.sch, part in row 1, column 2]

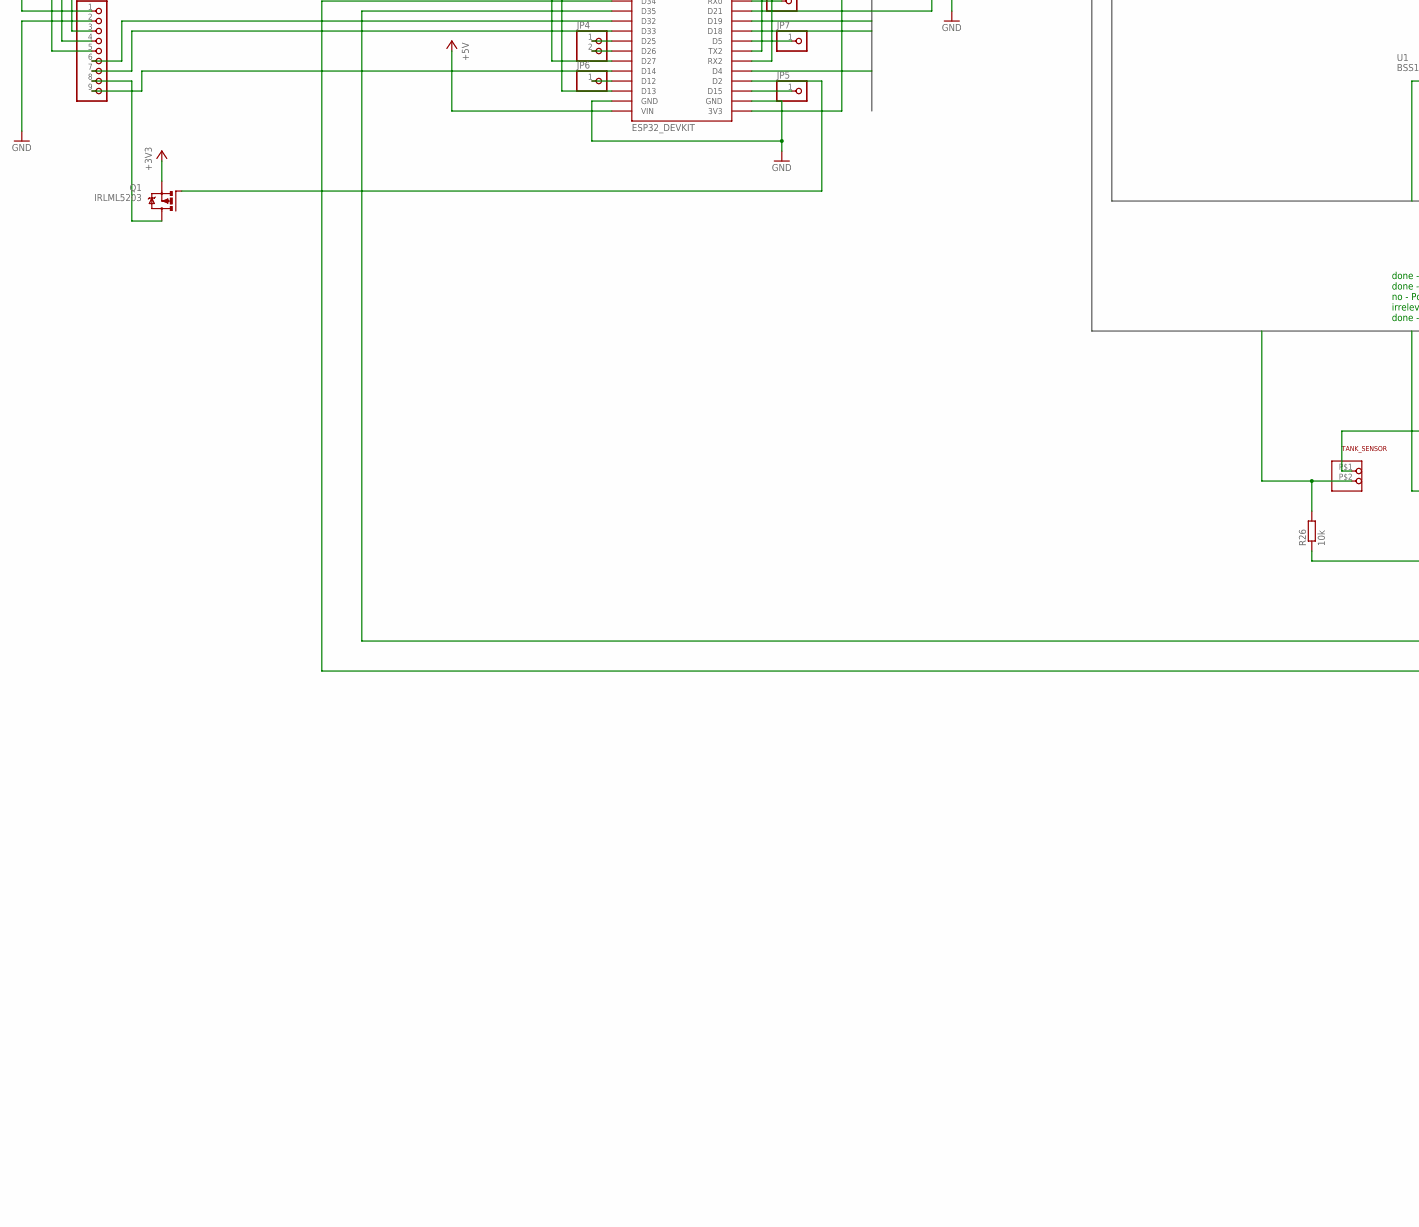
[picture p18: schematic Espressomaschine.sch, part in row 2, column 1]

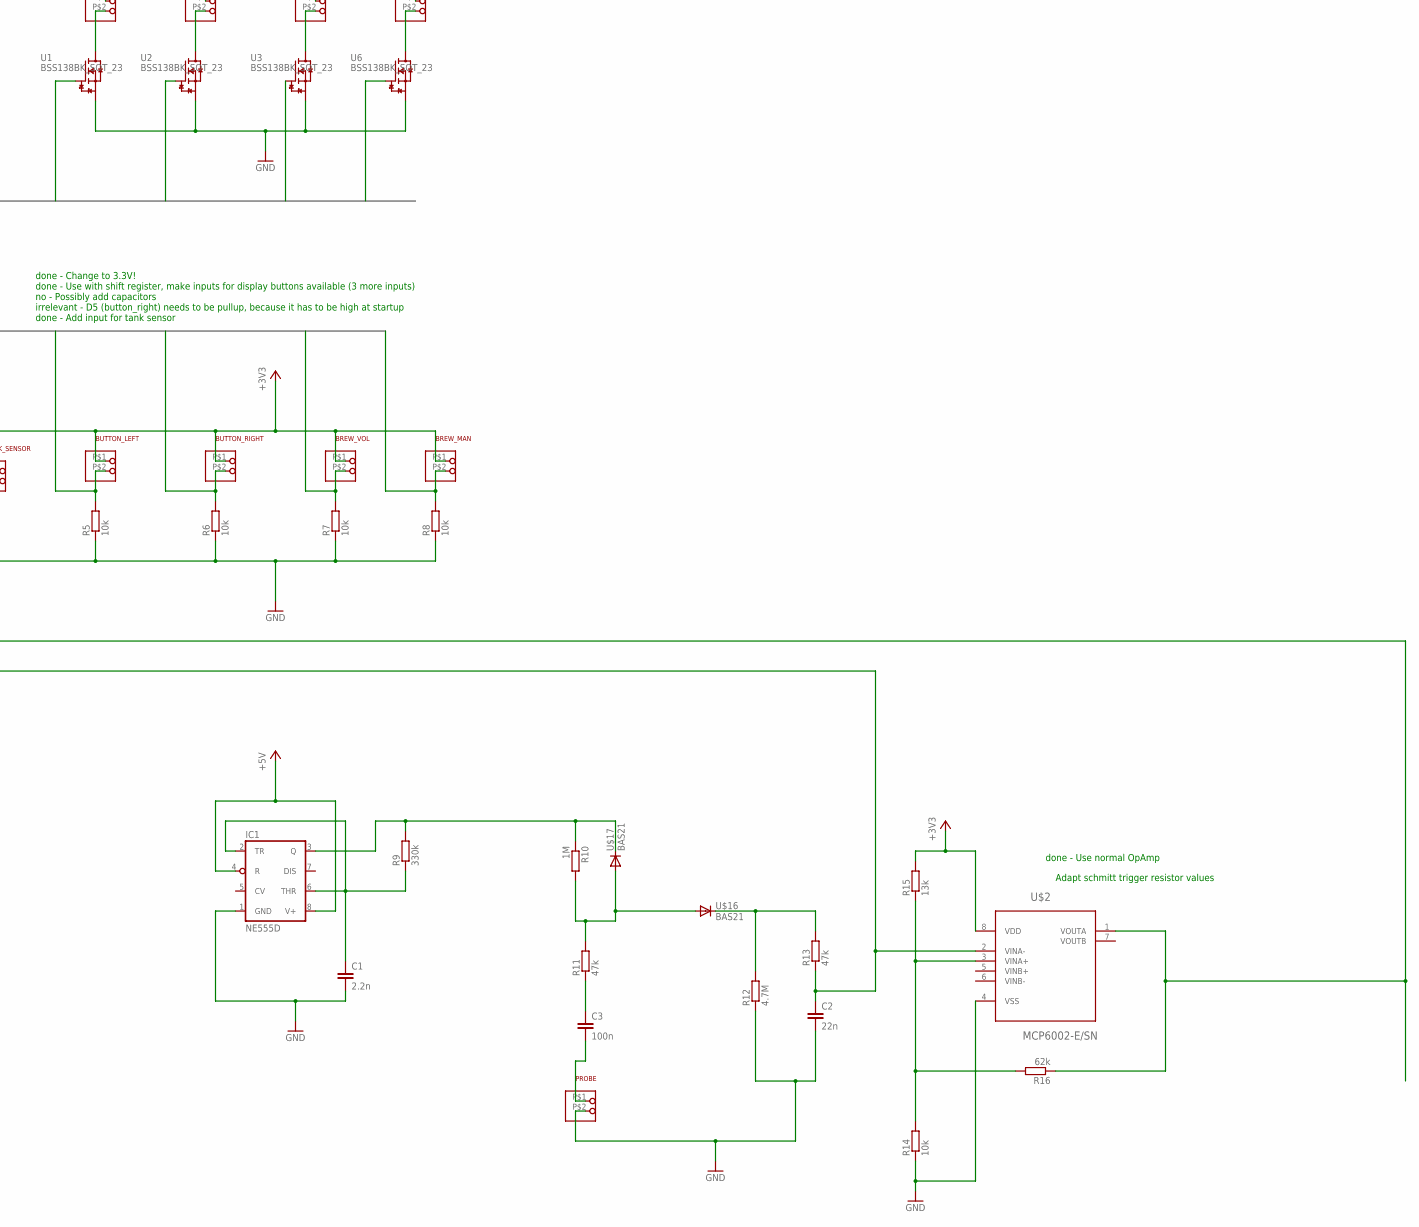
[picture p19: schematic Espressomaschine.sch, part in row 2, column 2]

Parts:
5V: 1X2RM5; 1X02_RM5
BOILER_HEATER: 1X2RM5; 1X02_RM5
BREW_MAN: 1X2RM5; 1X02_RM5
BREW_VOL: 1X2RM5; 1X02_RM5
BUTTON_LEFT: 1X2RM5; 1X02_RM5
BUTTON_RIGHT: 1X2RM5; 1X02_RM5
BU_HEATER: 1X2RM5; 1X02_RM5
C1: 2.2n; C0603
C2: 22n; C0603
C3: 100n; C0603
C4, C5: 10n; C0603
FLOW_PUMP: PINHD-1X3; 1X03
FLOW_RET: PINHD-1X3; 1X03
IC1: NE555D; SO08
IC5: MCP23017SO; SO28W
JP1: PINHD-1X6; 1X06
JP2, JP5, JP6, JP7: PINHD-1X1; 1X01
JP3: PINHD-1X9; 1X09
JP4, JP8: PINHD-1X2; 1X02
LED_LEFT: 1X2RM5; 1X02_RM5
LED_POWER: 1X2RM5; 1X02_RM5
LED_RIGHT: 1X2RM5; 1X02_RM5
LED_TANK: 1X2RM5; 1X02_RM5
PROBE: 1X2RM5; 1X02_RM5
Q1: IRLML5203; MICRO3
R1, R2, R3, R4: R-EU_R0603; R0603
R5, R6, R7, R8, R14, R26: 10k; R0603
R9, R22, R25: 330k; R0603
R10: 1M; R0603
R11, R13: 47k; R0603
R12: 4.7M; R0603
R15: 13k; R0603
R16: 62k; R0603
R20, R23: 4,7k; R0603
R21, R24: 220k; R0603
SJ1, SJ2, SJ3, SJ4: SJ
TANK_SENSOR: 1X2RM5; 1X02_RM5
TEMP_BOILER: PINHD-1X3; 1X03
TEMP_BU: PINHD-1X3; 1X03
TEMP_TUBE: PINHD-1X3; 1X03
U1, U2, U3, U4, U5, U6: BSS138BK_SOT_23; SOT23
U$1: ESP32_DEVKIT
U$2: MCP6002-E/SN; SOIC127P600X175-8N
U$16, U$17: BAS21; SOT23

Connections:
+3V3: BREW_MAN.P$1 (1), BREW_VOL.P$1 (1), BUTTON_LEFT.P$1 (1), BUTTON_RIGHT.P$1 (1), IC5.9 (VDD), IC5.15 (A0), IC5.18 (!RESET), Q1.2 (S), R15.2, TANK_SENSOR.P$1 (1), TEMP_BOILER.1, TEMP_BU.1, TEMP_TUBE.1, U$1.3V3, U$2.8 (VDD)
+5V: 5V.P$1 (1), BOILER_HEATER.P$1 (1), BU_HEATER.P$1 (1), FLOW_PUMP.1, FLOW_RET.1, IC1.4 (R), IC1.8 (V+), JP1.6, JP3.1, R1.2, R2.2, R3.2, R4.2, R20.2, R23.2, SJ1.2, SJ2.2, SJ3.2, SJ4.2, U$1.VIN
BOILER_HEATER: IC5.23 (GPA2), U4.1 (G)
BOILER_VALVE: IC5.1 (GPB0), JP1.4
BREW_MAN: BREW_MAN.P$2 (2), IC5.8 (GPB7), R8.2
BREW_VOL: BREW_VOL.P$2 (2), IC5.7 (GPB6), R7.2
BUTTON_LEFT: BUTTON_LEFT.P$2 (2), IC5.6 (GPB5), R5.2
BUTTON_RIGHT: BUTTON_RIGHT.P$2 (2), IC5.5 (GPB4), R6.2
BU_HEATER: IC5.22 (GPA1), U5.1 (G)
BU_VALVE: IC5.2 (GPB1), JP1.3
EXP_VALVE: IC5.4 (GPB3), JP1.1
GND: 5V.P$2 (2), C1.2, C2.2, C4.2, C5.2, FLOW_PUMP.2, FLOW_RET.2, IC1.1 (GND), IC5.10 (VSS), IC5.16 (A1), IC5.17 (A2), JP1.5, JP3.2, PROBE.P$2 (2), R5.1, R6.1, R7.1, R8.1, R12.1, R14.1, R22.1, R25.1, R26.1, TEMP_BOILER.3, TEMP_BU.3, TEMP_TUBE.3, U1.2 (S), U2.2 (S), U3.2 (S), U4.2 (S), U5.2 (S), U6.2 (S), U$1.GND@1 (GND), U$1.GND@2 (GND), U$2.4 (VSS)
LED_LEFT: IC5.25 (GPA4), U3.1 (G)
LED_POWER: IC5.26 (GPA5), U1.1 (G)
LED_RIGHT: IC5.28 (GPA7), U6.1 (G)
LED_TANK: IC5.27 (GPA6), U2.1 (G)
unnamed: LED_POWER.P$1 (1), R1.1, SJ1.1
unnamed: LED_TANK.P$1 (1), R2.1, SJ2.1
unnamed: LED_LEFT.P$1 (1), R3.1, SJ3.1
unnamed: Q1.1 (G), U$1.D2
unnamed: LED_RIGHT.P$2 (2), U6.3 (D)
unnamed: LED_LEFT.P$2 (2), U3.3 (D)
unnamed: BOILER_HEATER.P$2 (2), U4.3 (D)
unnamed: BU_HEATER.P$2 (2), U5.3 (D)
unnamed: LED_RIGHT.P$1 (1), R4.1, SJ4.1
unnamed: C1.1, IC1.2 (TR), IC1.6 (THR), R9.1
unnamed: R10.2, R11.2, U$16.1 (A), U$17.1 (A)
unnamed: C3.1, R11.1
unnamed: IC1.3 (Q), R9.2, R10.1, U$17.3 (C)
unnamed: R12.2, R13.2, U$16.3 (C)
unnamed: C2.1, R13.1, U$1.D34, U$2.2 (VINA-)
unnamed: R14.2, R15.1, R16.2, U$2.3 (VINA+)
unnamed: C3.2, PROBE.P$1 (1)
unnamed: R16.1, U$1.D35, U$2.1 (VOUTA)
unnamed: IC5.24 (GPA3), JP2.1
unnamed: JP7.1, U$1.D5
unnamed: LED_TANK.P$2 (2), U2.3 (D)
unnamed: IC5.12 (SCL), U$1.D22
unnamed: LED_POWER.P$2 (2), U1.3 (D)
unnamed: JP3.8, Q1.3 (D)
unnamed: JP4.1, U$1.D25
unnamed: JP3.3, U$1.TX2
unnamed: JP3.4, U$1.RX2
unnamed: JP3.5, U$1.D23
unnamed: JP3.6, U$1.D32
unnamed: JP3.7, U$1.D33
unnamed: JP3.9, U$1.D14
unnamed: C4.1, FLOW_RET.3, R20.1, R21.2
unnamed: C5.1, FLOW_PUMP.3, R23.1, R24.2
unnamed: IC5.13 (SDA), U$1.D21
unnamed: R21.1, R22.2, U$1.D27
unnamed: JP4.2, U$1.D26
unnamed: JP5.1, U$1.D15
unnamed: R24.1, R25.2, U$1.D13
unnamed: JP6.1, U$1.D12
unnamed: JP8.1, U$1.TX0
unnamed: JP8.2, U$1.RX0
PUMP: IC5.3 (GPB2), JP1.2
TANK_SENSOR: IC5.21 (GPA0), R26.2, TANK_SENSOR.P$2 (2)
TEMP_BOILER: TEMP_BOILER.2, U$1.D19
TEMP_BU: TEMP_BU.2, U$1.D4
TEMP_TUBE: TEMP_TUBE.2, U$1.D18

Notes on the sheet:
done - Change to 3.3V! done - Use with shift register, make inputs for display buttons available (3 more inputs) no - Possibly add capacitors irrelevant - D5 (button_right) needs to be pullup, because it has to be high at startup done - Add input for tank sensor
done - Change to any other pin than 2 (2 is connected to LED and should be an output pin)
done - Remove MOSFETs, SSR card only needs digital input done - Leave for Boiler and BU! done - Also update footprint!
done - Chose other pin, this one is pulled low
done- Add pin for display backlight control no - Change to library default pins
done - Use normal OpAmp
Adapt schmitt trigger resistor values

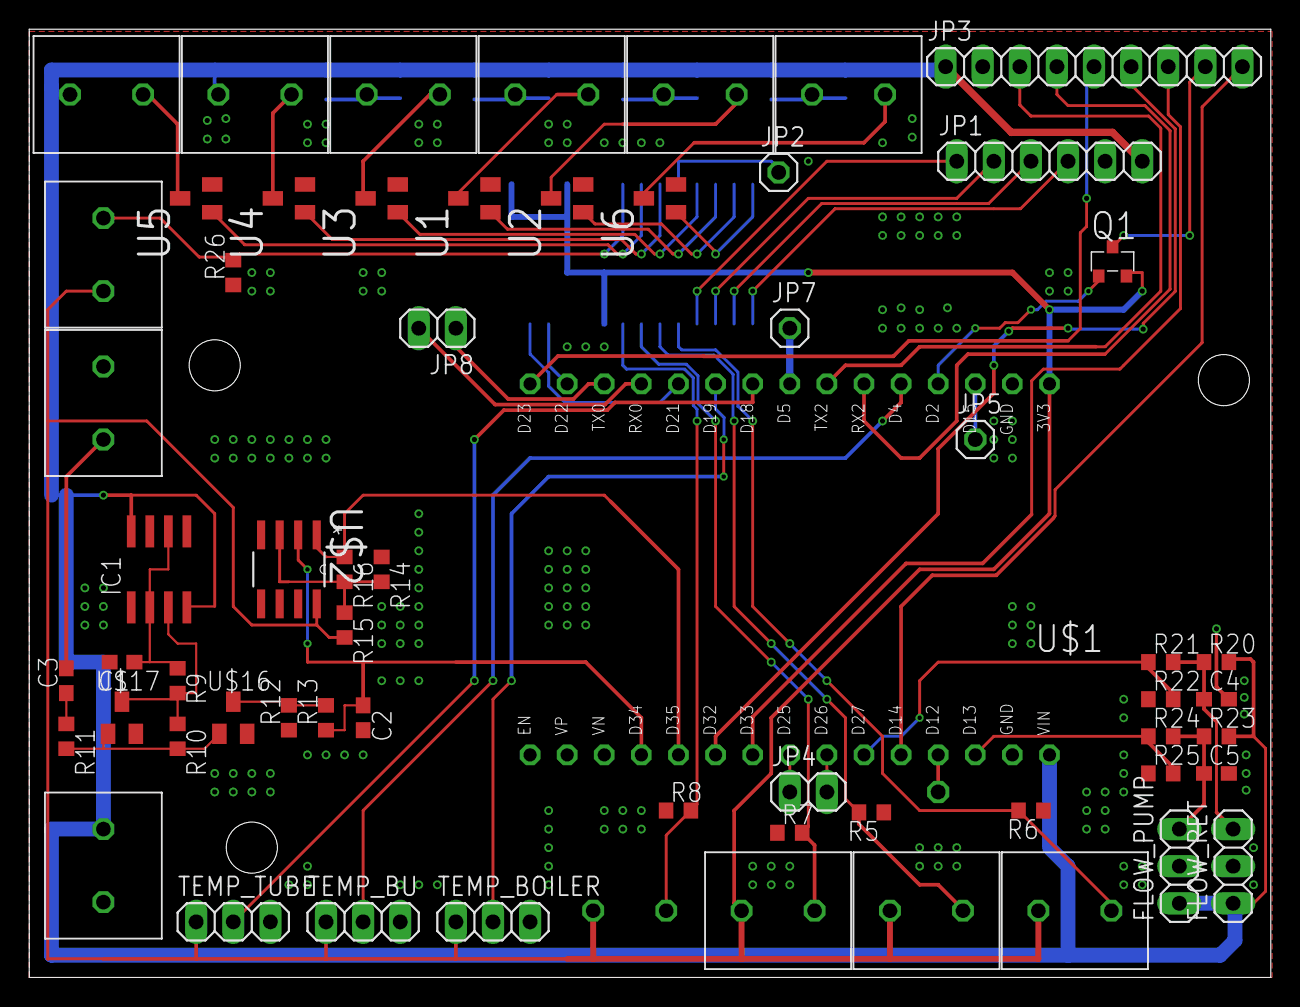
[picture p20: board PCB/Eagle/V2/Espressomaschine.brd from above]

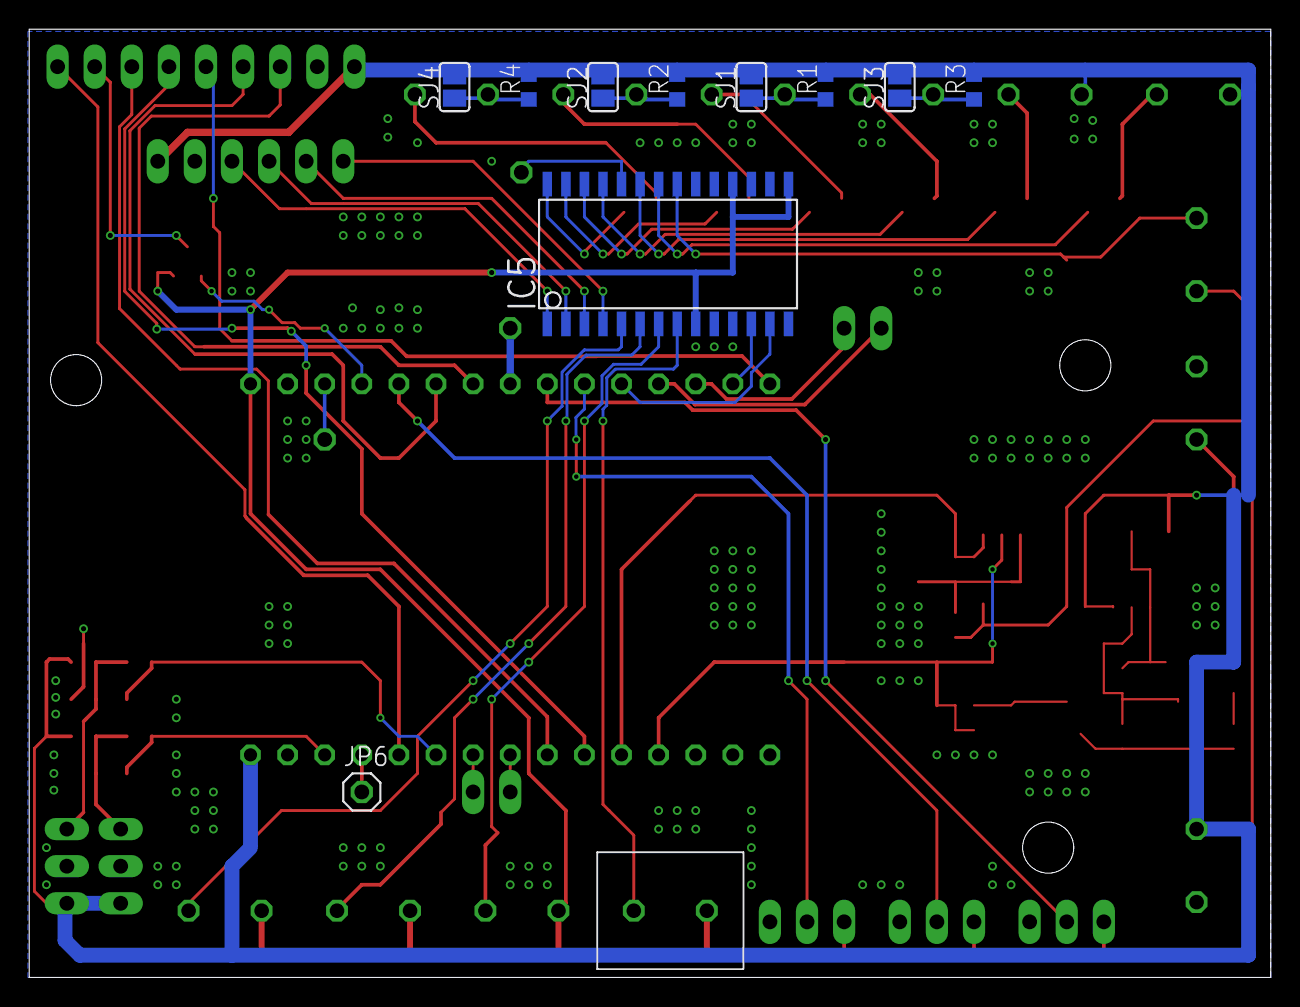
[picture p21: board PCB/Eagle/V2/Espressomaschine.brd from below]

Board: 2 copper layers, 85.0 x 64.9 mm, 71 parts (11 on the bottom side), 62 nets.

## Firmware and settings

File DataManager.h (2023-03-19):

/*
 * DataManager.h
 *
 *  Created on: Aug 20, 2020
 *      Author: tsugua
 */

#ifndef DATAMANAGER_H_
#define DATAMANAGER_H_

#include "Arduino.h"
#include "DeviceControl.h"
#include "WifiManager.h"

#define SSID_MAX_LEN				30
#define WIFI_PW_MAX_LEN				30
#define	HOST_NAME_MAX_LEN			30
#define LANG_MAX_LEN				5
#define BONJOUR_NAME_MAX_LEN		30


#define DEFAULT_TEMP_BOILER		121
#define	DEFAULT_TEMP_BU			85
#define	MAX_TEMP_BOILER			125
#define	MAX_TEMP_BU				110
#define	MIN_TEMP_BOILER			10
#define	MIN_TEMP_BU				10

#define	DEFAULT_FILL_BOILER_OVER_SONDE_TIME		5000
#define	DEFAULT_BOILER_FILL_MAX_TIME			120000
#define MAX_FILL_BOILER_OVER_SONDE_TIME
#define	MIN_FILL_BOILER_OVER_SONDE_TIME
#define MAX_BOILER_FILL_MAX_TIME
#define	MIN_BOILER_FILL_MAX_TIME

#define	DEFAULT_DISTRIBUTION_VOLUME				30
#define	MAX_DISTRIBUTION_VOLUME					200
#define	MIN_DISTRIBUTION_VOLUME					1
#define DEFAULT_VOLUME_OFFSET					40
#define	MAX_VOLUME_OFFSET						100
#define	MIN_VOLUME_OFFSET						0

#define	DEFAULT_BLYNK_ENABLED					true

#define	DEFAULT_BOILER_CONTROLLER_P				60
#define	MAX_BOILER_CONTROLLER_P					100
#define	MIN_BOILER_CONTROLLER_P					0.01
#define	DEFAULT_BU_CONTROLLER_P					60
#define	MAX_BU_CONTROLLER_P						100
#define	MIN_BU_CONTROLLER_P						0.01
#define DEFAULT_CONTROLLER_I					0.1
#define MAX_CONTROLLER_I						100
#define MIN_CONTROLLER_I						0
#define DEFAULT_CONTROLLER_D					0
#define MAX_CONTROLLER_D						100
#define MIN_CONTROLLER_D						0
#define DEFAULT_PUMP_TICK_TO_VOLUME_FACTOR		0.4585
#define DEFAULT_BYP_TICK_TO_VOLUME_FACTOR		0.4585
#define MIN_TICK_TO_VOLUME_FACTOR				0.001
#define	MAX_TICK_TO_VOLUME_FACTOR				10

#define DEFAULT_PREINFUSION_BUILDUP_TIME		4000
#define	MAX_PREINFUSION_BUILDUP_TIME			20000
#define	DEFAULT_PREINFUSION_WAIT_TIME			5000
#define	MAX_PREINFUSION_WAIT_TIME				20000

#define	IDLE_BLYNK_MIN_TEMP_UPDATE_INTERVAL		3000
#define	BREWING_BLYNK_MIN_TEMP_UPDATE_INTERVAL	500

#define DEFAULT_STANDBY_START_TIME				90*60*1000 // time after which standby mode will be entered if no user action
#define DEFAULT_STANDBY_WAKEUP_TIME				-1			//time in s after midnight at which the device will wake up from standby, -1 to disable wakeup

#define WIFI_CONNECT_INTERVAL					10000	//interval in which the device tries to connect to wifi
#define BLYNK_CONNECT_INTERVAL					10000	//interval in which the device tries to connect to the Blynk server. This is relevant, if WIFI is up, but internet is down


class DataManager {
public:
	static void pushTempBoiler(double temp);
	static void pushTempBU(double temp);
	static void pushTempTube(double temp);

	static double getTargetTempBoiler();
	static double getTargetTempBU();
	static void setTargetTempBoiler(double temp);
	static void setTargetTempBU(double temp);

	static long getFillBoilerOverSondeTime();
	static long getBoilerMaxFillTime();
	static double getDistributionVolume();
	static void setDistributionVolume(double volume);
	static double getVolumeOffset();
	static void setVolumeOffset(double offset);
	static double getBoilerControllerP();
	static void setBoilerControllerP(double p);
	static double getBoilerControllerI();
	static void setBoilerControllerI(double i);
	static double getBoilerControllerD();
	static void setBoilerControllerD(double d);
	static double getBUControllerP();
	static void setBUControllerP(double p);
	static double getBUControllerI();
	static void setBUControllerI(double i);
	static double getBUControllerD();
	static void setBUControllerD(double d);
	static double getPumpTickToVolumeFactor();
	static void setPumpTickToVolumeFactor(double f);
	static double getBypassTickToVolumeFactor();
	static void setBypassTickToVolumeFactor(double f);

	static int getPreinfusionBuildupTime();
	static void setPreinfusionBuildupTime(int time);
	static int getPreinfusionWaitTime();
	static void setPreinfusionWaitTime(int time);

	static void setStandbyStartTime(int time);
	static void setStandbyStartTime(const char* time);
	static int getStandbyStartTime();
	static String getStandbyStartTimeString();
	static unsigned long getStandbyWakeupTime();
	static void convertStandbyWakeupTimeToMachineTime();
	static String getStandbyWakeupTimeString();
	static void setStandbyWakeupTime(long time);
	static void setStandbyWakeupTime(const char* time);
	static bool getStandbyWakeupEnabled();
	static void incStandbyWakeupTimeByOneDay();

	static bool getWifiEnabled();
	static void setWifiEnabled(bool enabled);

	static bool getWifiConnected();
	static bool getHotspotMode();

	static String setWIFICredentials(const char* newSSID, const char* newPassword, const char* newHostName);
	static String getWifiSSID();
	static String getWifiPassword();
	static String getWifiHostName();
	static String getLanguage();
	static String getBonjourName();
	static void setLanguage(const char* language);
	static void setBonjourName(const char* name);

	static void init();
	static void update();
private:
	DataManager(){}
	virtual ~DataManager(){}

	static DeviceControl *dev;
	static WifiManager *wifiMan;

	static double targetTempBoiler;
	static double targetTempBU;

	static long fillBoilerOverSondeTime;
	static long boilerMaxFillTime;

	static double distributionVolume;
	static double volumeOffset;

	static double boilerControllerP;
	static double boilerControllerI;
	static double boilerControllerD;
	static double BUControllerP;
	static double BUControllerI;
	static double BUControllerD;
	static double pumpTickToVolumeFactor;
	static double bypassTickToVolumeFactor;

	static int preinfusionBuildupTime;
	static int preinfusionWaitTime;
	static unsigned long standbyWakeupTime;
	static int standbyStartTime;	//time after wich standby mode will be entered
	static bool standbyWakeupEnabled;	//used to disable wakeup functionality

	static char wifiSsid[SSID_MAX_LEN+1];
	static char wifiPassword[WIFI_PW_MAX_LEN+1];
	static char wifiHostName[HOST_NAME_MAX_LEN+1];
	static bool wifiEnabled;
	static char language[LANG_MAX_LEN+1];
	static char bonjourName[BONJOUR_NAME_MAX_LEN+1];

	static uint32_t calculateWIFIChecksum();
	static void eepromWrite(uint8_t *src, int addr, int len, bool commit);
	static void eepromRead(uint8_t *dst, int addr, int len);

	static bool scheduleRestart;
	static bool standbyWakeupTimeConverted;

	static unsigned long lastWifiConnectTryTime;
};
#endif /* DATAMANAGER_H_ */

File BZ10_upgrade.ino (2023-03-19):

#include "SPIFFS.h"
#include "Arduino.h"
#include "BoilerStateMachine.h"
#include "BUStateMachine.h"
#include "BrewStateMachine.h"
#include "DisplayStateMachine.h"
#include "MachineStatusStateMachine.h"
#include "DeviceControl.h"
#include "DataManager.h"
#include "Webserver.h"
#include "WifiManager.h"

//The setup function is called once at startup of the sketch

BoilerStateMachine *boilerSM;
BUStateMachine *brewingUnitSM;
BrewStateMachine *brewSM;
DisplayStateMachine *dispSM;
MachineStatusStateMachine *machineStatSM;
DeviceControl *dev;
WifiManager *wifiMan;

void setup()
{
	Serial.begin(115200);
	if(!SPIFFS.begin(true)){
		Serial.println("An Error has occurred while mounting SPIFFS");
		return;
	}
	dev = DeviceControl::instance();
	DataManager::init();
	machineStatSM = MachineStatusStateMachine::instance();
	boilerSM = new BoilerStateMachine();
	brewingUnitSM = new BUStateMachine();
	brewSM = new BrewStateMachine();
	dispSM = new DisplayStateMachine(brewSM);
	wifiMan = WifiManager::instance();

	Serial.println("Espresso machine initialized");
}

void loop()
{
	machineStatSM->update();
	boilerSM->update();
	brewingUnitSM->update();
	brewSM->update();
	dispSM->update();
	DataManager::update();
	dev->update();
	wifiMan->update();

	static bool webserverInitialized = false;
	if(DataManager::getWifiEnabled() && !webserverInitialized){
		//webserver only has to be initialized and then runs on its own
		Webserver::instance()->init();
		webserverInitialized = true;
	}
	if(dev->getButton1LongPressed()){
		DataManager::setWifiEnabled(!DataManager::getWifiEnabled());
	}
}

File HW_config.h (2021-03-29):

/*
 * device_config.h
 *
 *  Created on: May 30, 2020
 *      Author: tsugua
 */

#ifndef HW_CONFIG_H_
#define HW_CONFIG_H_

#include "ADS1115_WE.h"

#define SR_SER				22
#define	SR_SCK				19
#define	SR_RCK				21

#define MCP_SCL				22
#define MCP_SDA				21
#define MCP_ADDR			0x21
#define ADS_ADDR			0x48
#define ADS_RDY				12
#define ADS_SAMPLE_INTERVAL	100		//sample interval in ms

#define	BU_VALVE			9
#define BU_VALVE_LOW_LEVEL_TRIGGER
#define	BOILER_VALVE		8
#define BOILER_VALVE_LOW_LEVEL_TRIGGER
#define	PUMP				10
#define PUMP_LOW_LEVEL_TRIGGER
#define	BOILER_HEATER		2
//#define BOILER_HEATER_LOW_LEVEL_TRIGGER
#define	BU_HEATER			11
#define BU_HEATER_LOW_LEVEL_TRIGGER
#define	EXP_VALVE			1
#define EXP_VALVE_LOW_LEVEL_TRIGGER

#define	LED_LEFT			4
#define	LED_POWER			5
#define	LED_TANK			6
#define	LED_RIGHT			7

#define BOILER_TEMP_ON_ADS	//comment to use TSIC for boiler temperature
#define ADS_BOILER_INPUT	ADS1115_COMP_0_GND
#define ADS_BOILER_MAX_VOLT	ADS1115_RANGE_4096
#define ADS_VCC_INPUT		ADS1115_COMP_1_GND
#define ADS_VCC_MAX_VOLT	ADS1115_RANGE_2048
#define ADS_VCC_CONV_FACTOR	2	//(R27+R28)/R28
#define ADS_BOILER_REF_R	22e3	//R29
//calculate NTC temperature:	(see Wikipedia)
// 1/T = 1/TN + 1/B*ln(RT/RN) with
// T:	temperature
// TN:	reference temperature
// B:	conversion factor
// RT:	NTC resistance at T
// RN:	NTC resistance at TN
#define ADS_BOILER_B		4458	//factor for calculation of NTC temperature
#define ADS_BOILER_TN		373.15	//reference temperature: 100 degree celsius
#define ADS_BOILER_RN		1.12e3	//resistance at TN
#define ADS_T0				273.15	//0 degree celsius in Kelvin for convenience
//TSIC pins:
#define	TEMP_BOILER_PIN		19
#define	TEMP_BU_PIN			4
#define	TEMP_TUBE_PIN		18

#define	BUTTON_LEFT_PIN		13
#define	BUTTON_RIGHT_PIN	12
#define	BREW_VOL_PIN		14
#define	BREW_MAN_PIN		15
#define TANK_PIN			0

#define	FLOW_PUMP_PIN		13
#define	FLOW_RET_PIN		27

#define	PROBE_ANALOG_PIN	34
#define	PROBE_DIGITAL_PIN	35

#define TFT_DC 		23
#define TFT_CS 		17
#define	TFT_MOSI	32
#define	TFT_CLK		33
#define	TFT_MISO	14
#define TFT_RST		16
#define TFT_LED		2

#endif /* HW_CONFIG_H_ */

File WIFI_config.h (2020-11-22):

/*
 * WIFI_config.h
 *
 *  Created on: Nov 22, 2020
 *      Author: tsugua
 */

#ifndef WIFI_CONFIG_H_
#define WIFI_CONFIG_H_


#define	DEFAULT_SSID		"Espresso"
#define	DEFAULT_PASSWORD	"CoffeeLove"
#define	DEFAULT_HOST_NAME	"BZ 10"

#define	BLYNK_AUTH_KEY		"**enter your own auth key here**"


#endif /* WIFI_CONFIG_H_ */

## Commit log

2020-08-25 fixed displayed temperatures
2020-08-30 Added P controller behavior for both heaters
2020-09-19 Added flowmeter support
2020-10-02 Added temperature error state
    [DeviceControl.cpp, TSIC.cpp]
2020-10-02 Added error message on display for temperature sensor error
    [DeviceControl.cpp, DisplayStateMachine.h]
2020-10-02 disabling heaters in standbye and on errors
    [DeviceControl.cpp]
2020-10-13 Workaround for right button only working as pullup
    [DeviceControl.cpp]
2020-12-16 added build variable or boiler heater quick start. Disabled quick start
2020-12-16 Made flow sensor tick to volume conversion rates adjustable through Blynk
2020-12-16 Updated default values for boiler heater and flow sensors
2020-12-23 first try for debouncing buttons
2020-12-23 Better button debouncing
2021-02-10 Change: PID instead of P controller
2021-02-18 Added PCB files
    [Espressomaschine.brd, Espressomaschine.sch]
2021-02-23 Added LTSpice simulation for boiler probe
2021-03-03 PCB for for external antenna and with NTC connectors
    [Espressomaschine.brd, Espressomaschine.sch]
2021-03-04 Finalized PCB V3
    [Espressomaschine.brd, Espressomaschine.sch]
2021-03-29 ADD: ADS1115 for boiler temperature measurement
2022-04-30 CHANGE: Fixed getting stuck in Blynk loop when internet down
    Replaced the blocking Blynk.connect() with a non-blocking version, that
    also is non-blocking, if wifi is available but the internet is down.
    [DataManager.cpp, DataManager.h]
2023-03-18 switched from Blynk to webserver
